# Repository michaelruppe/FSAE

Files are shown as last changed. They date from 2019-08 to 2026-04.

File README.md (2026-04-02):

# FSAE

Hardware projects for the FSAE Electric 2019/2020 competition (Australia).
💻Github https://github.com/michaelruppe/FSAE

## Resources
**Team mentoring and design reviews available - contact through [michaelruppe.com](https://michaelruppe.com)**

[ShutdownCircuit.com](https://shutdowncircuit.com) is a free resource to help new FSAE EV teams shortcut the growing pains of designing EV safety systems.

## [TSAL](TSALv3)
A light that indicates presence of dangerous voltage within the Tractive System

<div align="center">
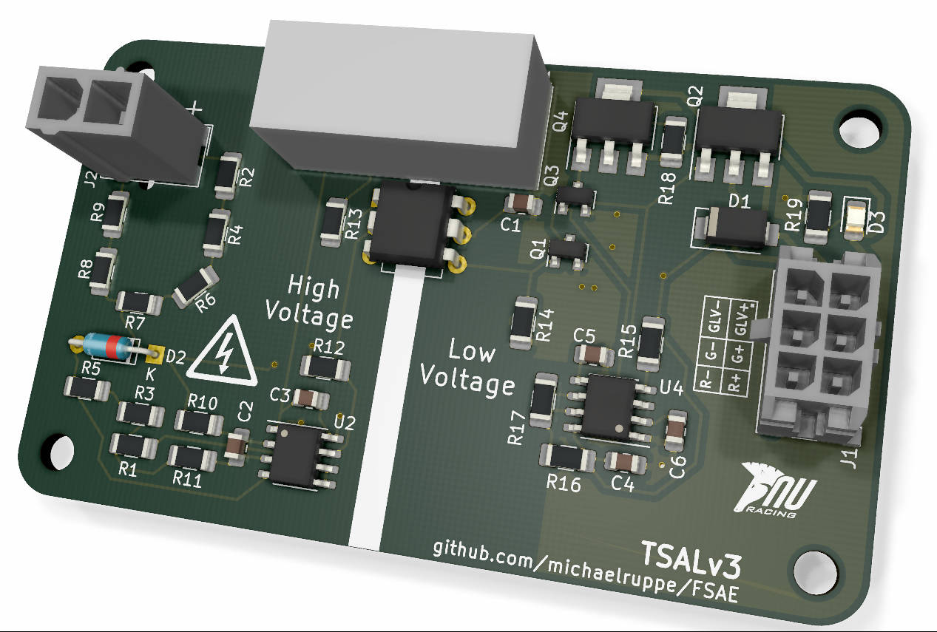
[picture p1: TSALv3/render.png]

<p>The third iteration of the TSAL driver. </p>
</div>

Watch a [video walkthrough](https://youtu.be/bgW9xbbovIY) explaining the circuit operation and design decision.

## [Precharge](Precharge)
A device to precharge the Tractive System. This prototype features voltage feedback to protect AIRs. In open-loop systems, if a wiring fault develops - eg. precharge resistor is disconnected - then the precharge is ineffective and AIRs may become damaged.
<div align="center">
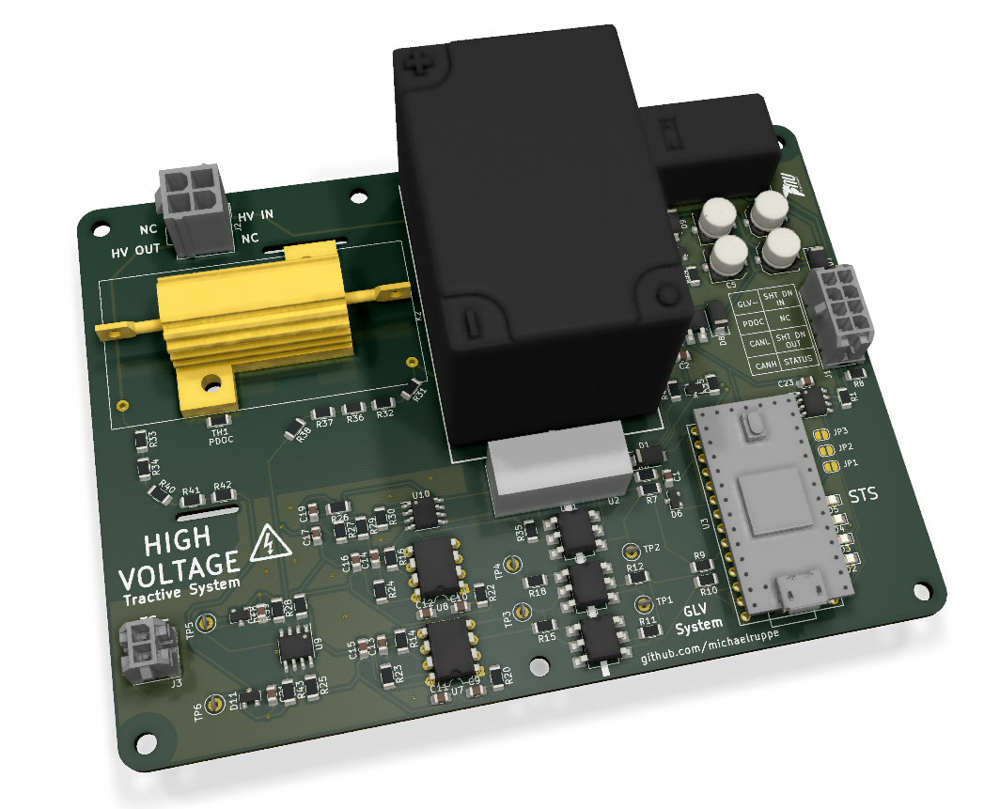
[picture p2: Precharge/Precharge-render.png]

<p>The prototype Precharge module</p>
</div>

 ## [HFL (Hard Fault Latch)](HFL)

 Latches momentary faults that are required to shutdown the EV.

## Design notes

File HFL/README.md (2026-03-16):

**Warning: This design was never physically prototyped. As-is it is a mostly-complete design, but has never been through build, commissioning, troubleshooting. Proceed at your own risk.**

# Hard Fault Latch
A shutdown-circuit component.

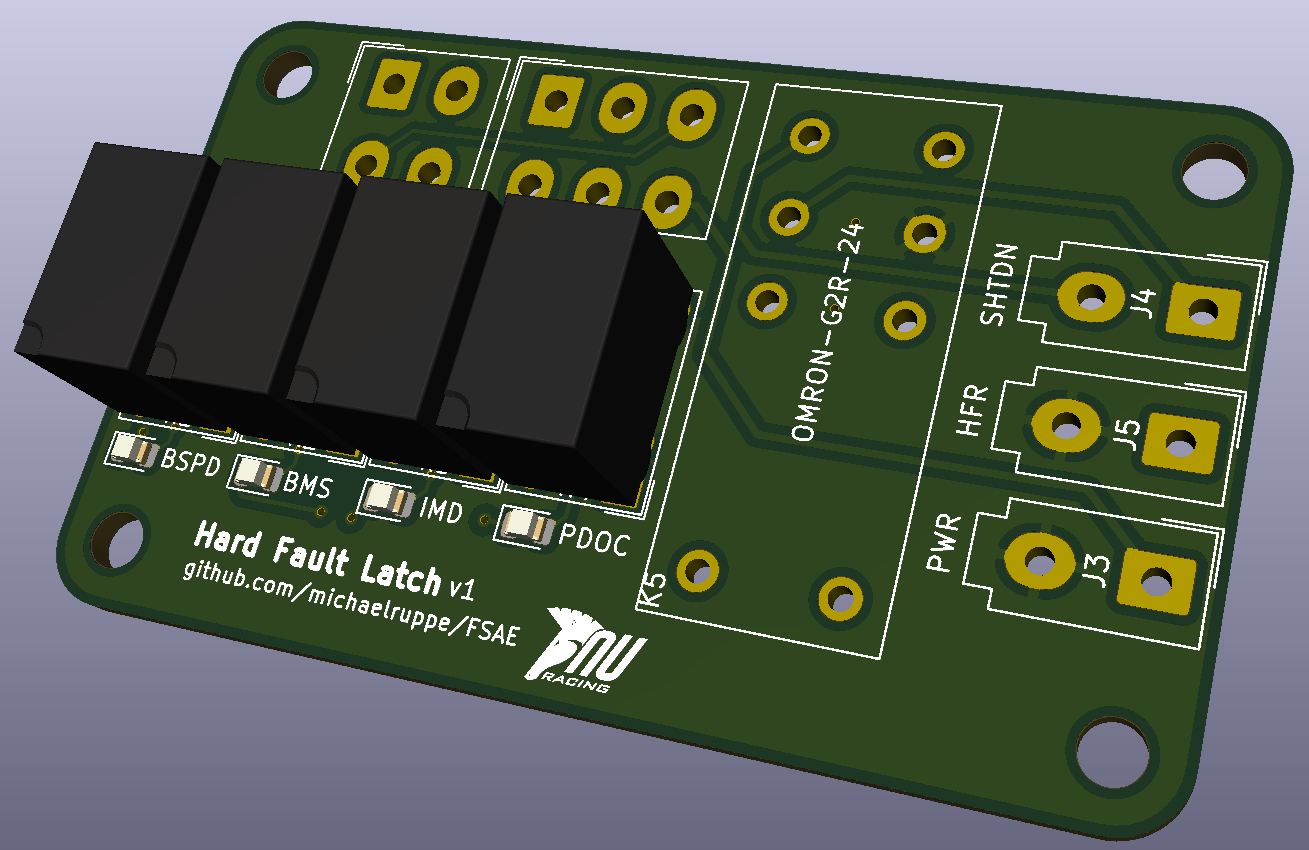
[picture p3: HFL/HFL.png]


The **Hard Fault Latch (HFL)** is a device that breaks the *Shutdown Circuit* when a *Hard Fault* is detected. These are faults generated by the IMD, BMS, BSPD PDOC-temperature, and BOTS. A Hard Fault is any fault that will deactivate the Tractive System, and cannot be reset by the driver.
The HFL is built upon relay-logic because it is easy to understand, reliable and hardened against noise and voltage transients.

An operator must press the HFR button each time the vehicle is powered-on, before the Tractive System can be activated.

Additionally, the HFL passes hard-fault statuses for the IMD, BMS, BSPD and PDOC (**not** BOTS) to the CCU for logging and dash-display.

# Technical Specifications
**ToDo**

# Design Justification
The final output relay must be capable of carrying sufficient current to power an AIR, and be a DPDT type. The smallest readily-available relay found was an OMRON G2R which is rated for 5A.

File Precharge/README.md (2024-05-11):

# Precharge

**[Watch the walkthrough video](https://www.youtube.com/watch?v=6-RndXZ5mR4)**

A device to precharge the Tractive System. This prototype features voltage feedback to protect AIRs. In open-loop systems, if a wiring fault develops (eg. precharge resistor is disconnected or discharge is stuck on) then the precharge is ineffective and AIRs may become damaged.
<div align="center">

<p>Figure 1: The prototype Precharge module</p>
</div>

**Important Directories / Files**
- [code/precharge](code/precharge) - The source code
- [docs/schematic-v1.1.pdf](docs/schematic-v1.1.pdf) - The schematic, as built.
- [docs/pinout-v1.1.pdf](docs/pinout-v1.1.pdf) - Pinout diagram with connection descriptions.
- [docs](docs) - Data collected during commissioning, image assets for this document.
- [Precharge](Precharge) - The PCB design files

## Contents

- [Specifications and Features](#Specifications-and-Features)
- [Operation](#Operation)
- [Commissioning Steps - Precharge](#Commissioning-Steps-Precharge)
  - [Characterise Voltage-Frequency Relationship](Characterise-Voltage-Frequency-Relationship)
  - [Simulate Precharge](#Simulate-Precharge)
  - [Results](#Results)
- [Commissioning Steps - PDOC](#Commissioning-Steps-PDOC)
- [How to modify this design](#How-to-modify-this-design)
- [Recommendations](#Recommendations)

## Specifications and Features
- Wide input voltage 0 - 600V
- Powered by shutdown circuit: 12V
- Integrated PDOC
- Isolated HV measurement
- CAN interface (provisional) for status output
- Serial interface for status and commissioning data
- FSAE one-size-fits-all. This module is capable of precharging any voltage accumulator (within FSAE rules) without significant hardware/software rework. To modify for a new accumulator/tractive-system, select appropriate precharge resistor and update relevant software parameters, discussed in [How to modify this design](#How-to-modify-this-design)

## Operation
A brief description of the Precharge logic follows. Refer to *Figures 2 & 3* for state-flow information.
- Initialise in `State: Standby` and monitor for a stable Shutdown Circuit.
- If Shutdown Circuit is stable, enter `State: Precharge`:
  - Close the precharge relay
  - Monitor Accumulator voltage and Tractive System voltage
  - Once TSV is close enough to AV (eg >95%), precharge is complete
  - If precharge is too fast or too slow, a fault is likely present eg. Wiring fault, discharge stuck-on, stuck relay.
- If precharge completed with no errors, proceed to `State: Online`:
  - Enable the AIR, open precharge relay

If at any point the Shutdown Circuit voltage becomes too low, enter `State: Standby`

<div align="center">
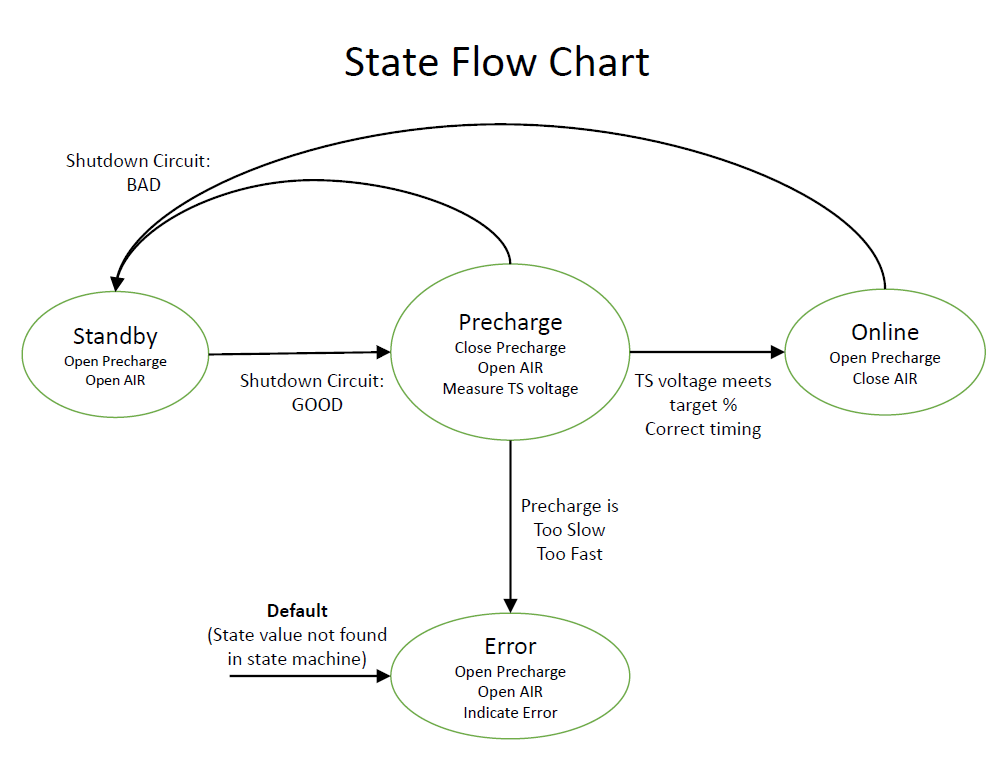
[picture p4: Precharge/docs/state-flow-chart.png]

<p>Figure 2: A top-level look at the state-flow behaviour</p>
</div>
<div align="center">
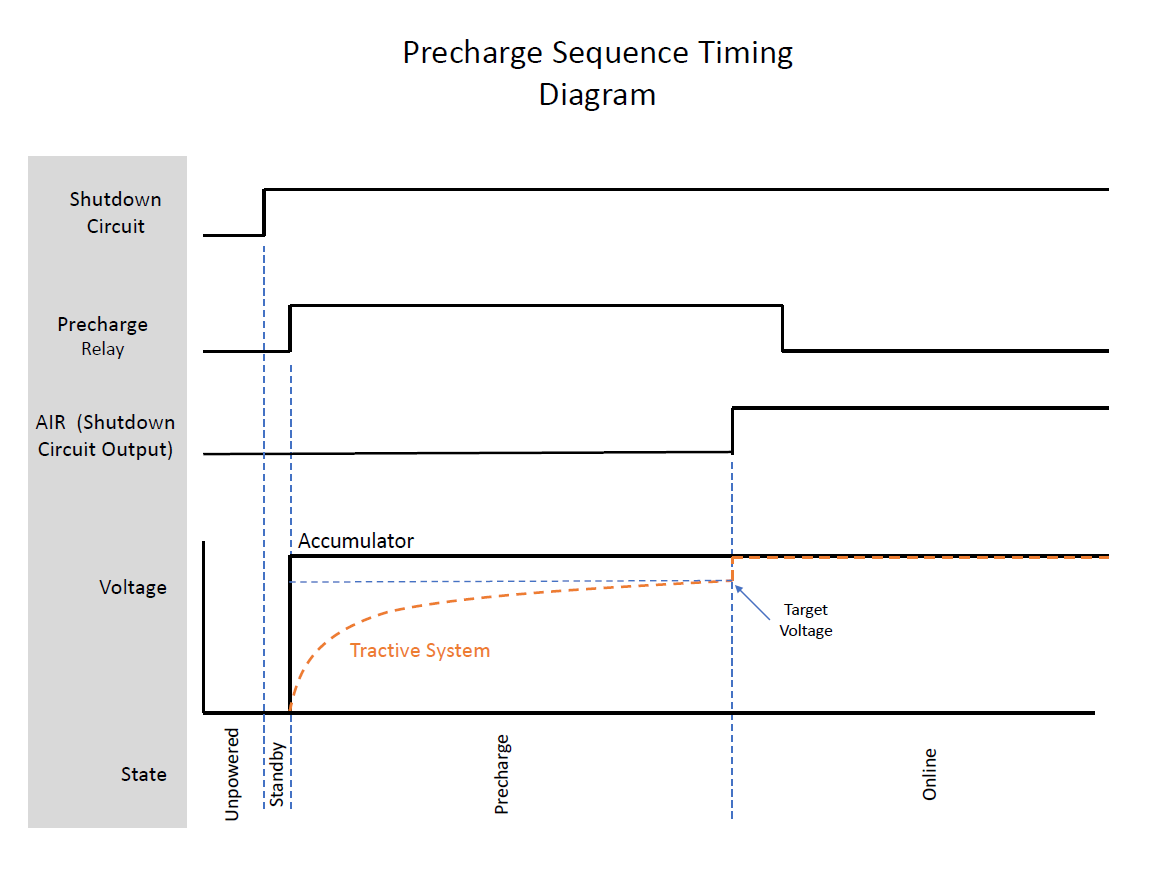
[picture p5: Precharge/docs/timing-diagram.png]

<p>Figure 3: precharge sequence timing. When the TS voltage reaches the target voltage, precharge is complete and the AIR closes. The target voltage should be 90-95% of the Accumulator voltage</p>
</div>

## Commissioning Steps - Precharge
*Refer to the [docs/schematic-v1.1](docs/schematic-v1.1.pdf) for component and test-point references.*

*Refer to [docs/Experiments.xlsx](docs/Experiments.xlsx) for sample data collected during prototype construction.*

This section describes the steps taken to construct and characterise the Precharge Module. Repeat these steps as necessary when re-commissioning later versions of the circuit.

### Characterise Voltage-Frequency Relationship
- Assemble power supply components and V-F converter circuitry `U5 - U9`.
- Characterise voltage-frequency performance: perform V-F experiment `code/01-v-f-experiment` *Refer to Figure 4 for sample data collected during prototype construction*
  - Apply 0.15-10V at V-F inputs: `TP5, TP6`.
  - Record output frequencies: `TP1, TP2` vs input voltages.
  - Create linear fit and record the gain and offset parameters.
  - Update [code/precharge/measurements.cpp](code/precharge/measurements.cpp) with the linear-fit parameters: `V2F_slope_accu, V2F_ofs_accu, V2F_slope_ts, V2F_ofs_ts`
- If resistors `R31,R32,R36-39` or `R33,R34,R40-R3` are different to schematic:
  - Find the gain of these voltage dividers: eg `Gain = R39/(R31+R32+R36+R37+R38+R39)`
  - Update [code/precharge/measurements.cpp](code/precharge/measurements.cpp): `gainVoltageDivider` with the new gain value.

  <div align="center">
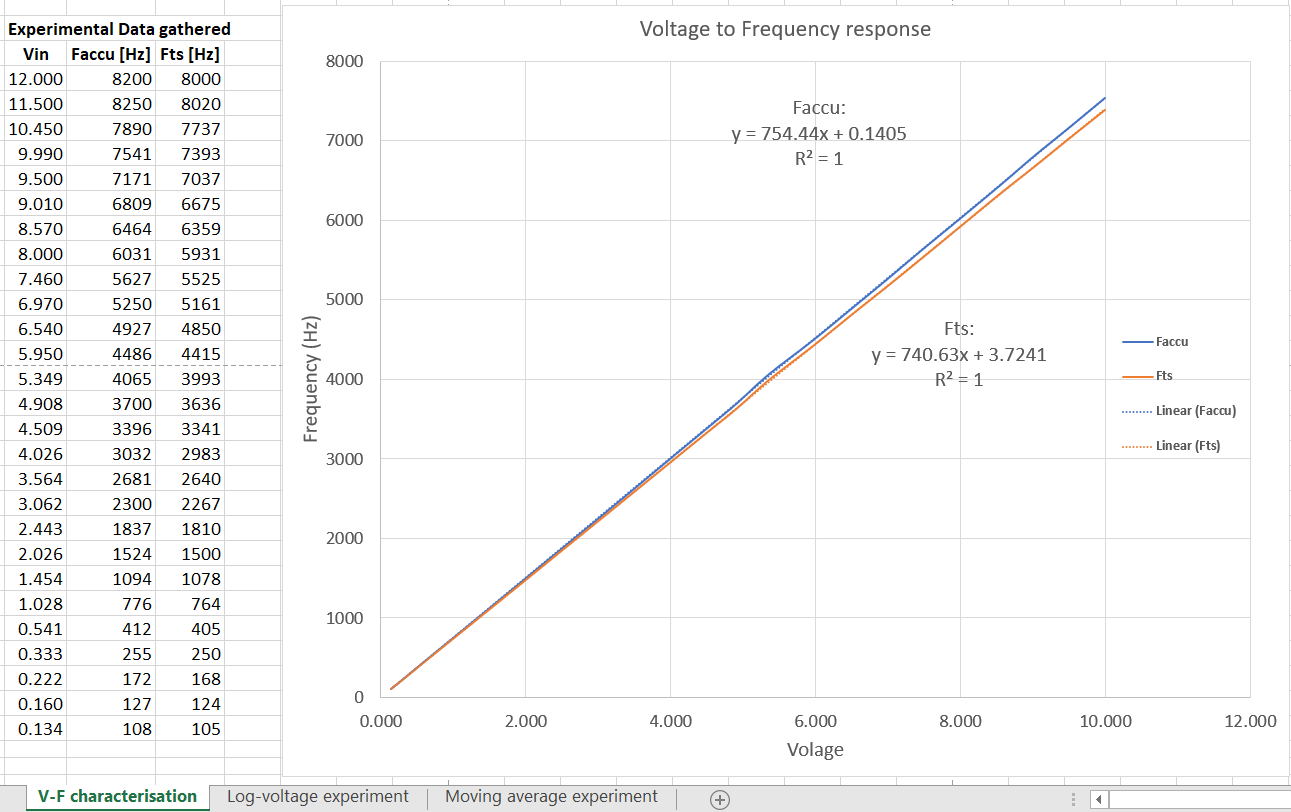
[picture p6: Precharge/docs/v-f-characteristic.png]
  
  <p>Figure 4: Results from the V-F experiment - data collected from the prototype during construction. The V-F response is extremely linear. Expect f(0V) = 0Hz, which is supported by very small y-intercept constants. While the V-F converter circuits are nominally identical, they should be characterised separately to account for component tolerance.</p>
  </div>

### Simulate Precharge
Here, we simulate a precharge sequence using low voltages that bypasses the prescaling voltage dividers.

<div align="center">
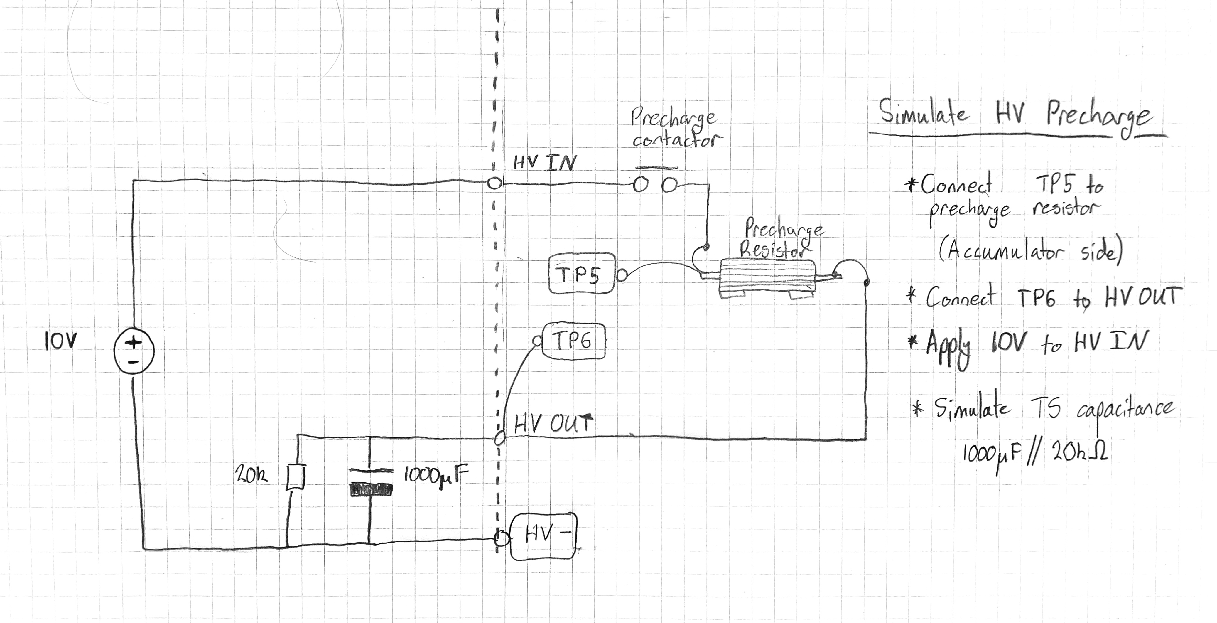
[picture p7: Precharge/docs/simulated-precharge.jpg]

<p>Figure 5: Simulate a precharge sequence using a low voltage. The prescaling voltage dividers are bypassed by connecting Testpoint:TP5 to the switched accumulator voltage; and Testpoint:TP6 to the HV OUT connector.
</p>
</div>

*Voltages listed are referenced to the `GNDS` net, connector `J3` labelled `TS-`*
- Connect a known capacitive load eg 1000uF to `HV OUT`. Include a large parallel resistance (eg 20k) for capacitor discharge.
  - The voltage divider created by this resistance and the precharge resistor `R46` will limit the maximum voltage seen at capacitor. Large resistances will reduce this effect, but the capacitor will discharge more slowly during this test.
- Bypass the prescaling voltage dividers:
  - Connect `TP5` to precharge resistor (accumulator side)
  - Connect `TP6` to `HV OUT`
- Apply 4-10V to `HV IN`. Exact voltage will depend on accumulator voltage to be simulated: Accumulator Voltage multiplied by `gainVoltageDivider` (0.015 from prescribed components) gives this voltage.
- Monitor serial data from the microcontroller via USB
- Power the circuit at `J1`
- Monitor precharge behaviour in serial console and note precharge percentage and duration.
- Modify and upload [code/precharge/precharge.ino](code/precharge/precharge.ino) as necessary. Relevant parameters are:
  - `MIN_EXPECTED`[ms] The minimum allowable precharge time. Times faster than this are likely due to wiring fault.
  - `MAX_EXPECTED`[ms] The maximum allowable precharge time. Times slower than this are likely due to wiring fault, stuck discharge circuit.
  - `TARGET_PERCENT`[%] Precharge to this percentage of accumulator voltage.
    - The discharge resistance used during this simulation affects the maximum TS voltage attainable. I found a maximum voltage of only 90% when using Precharge:390Ohm and discharge 4k7.

### Results
A precharge sequence was simulated following the above procedure with results shown in *Figure 6*. Simulated voltages were measured accurate to the nearest volt.

**Parameters:**
- V Accumulator: 5.05V (336V equivalent)
- Tractive system capacitor: 1000uF
- Tractive system discharge capacitor: 4k7 (connected in parallel with capacitor. Larger value as in Figure 5 is preferred)
- `gainVoltageDivider`= 0.015 ([code/precharge/measurements.cpp](code/precharge/measurements.cpp))
- Target precharge percentage: 88.0 (discharge resistor is only one order of magnitude larger than 390Ohm precharge resistor)

<div align="center">
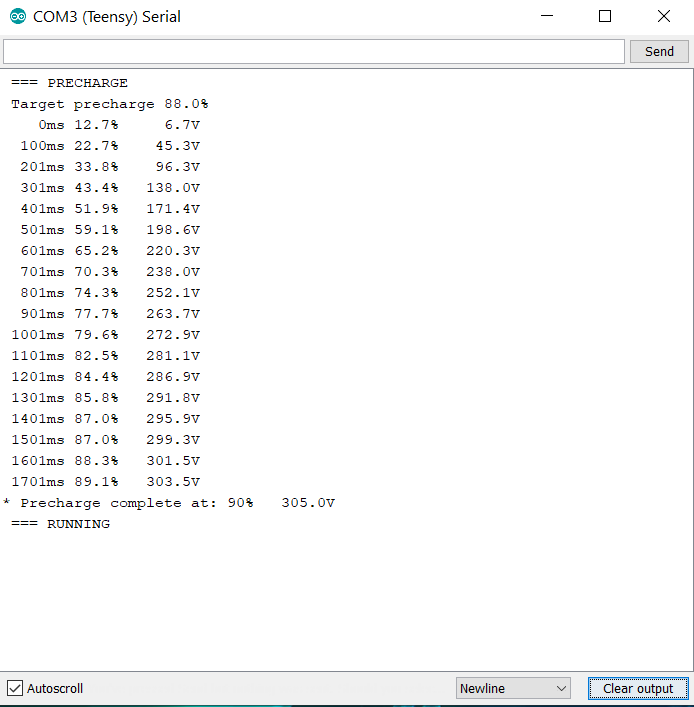
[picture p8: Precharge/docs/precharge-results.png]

<p>Figure 6: Results from a simulated precharge. Here, the accumulator was simulated with 5.05V => 337Vequiv. The TS voltage at TP6 reached 4.561V => 304Vequiv. which is 90.2% as indicated. The precharge finished at 90% instead of 88% because some settling time is imposed by the program.
</p>
</div>

Of note are the seemingly high precharge percentages observed between 0-200ms. These are artifacts of moving average filters used to smooth voltage measurements and reject spurious measurements. Since the smoothed accumulator voltage does not rise instantaneously, the precharge voltage represents a significant percentage in early stages of the precharge cycle.

## Commissioning Steps - PDOC
The Precharge module includes an integrated thermal overload protection (PDOC) (Figure 7). A thermistor `TH1` monitors the precharge resistor temperature. As temperature increases, the inverting-input voltage of comparator `U10A` rises. Once the voltage at the inverting input rises above the reference voltage (noninverting input) the PDOC will trip. The reference voltage created by `R26` and `R27` therefore sets the temperature threshold. If `R27` = `R29` then select `R26` to be equal to the value of `TH1` at the desired trip-temperature. Referring to thermistor data in Figure 8, for a trip-temperature of eg. 80 degC, `R26` should be about 12kOhm.

<div align="center">
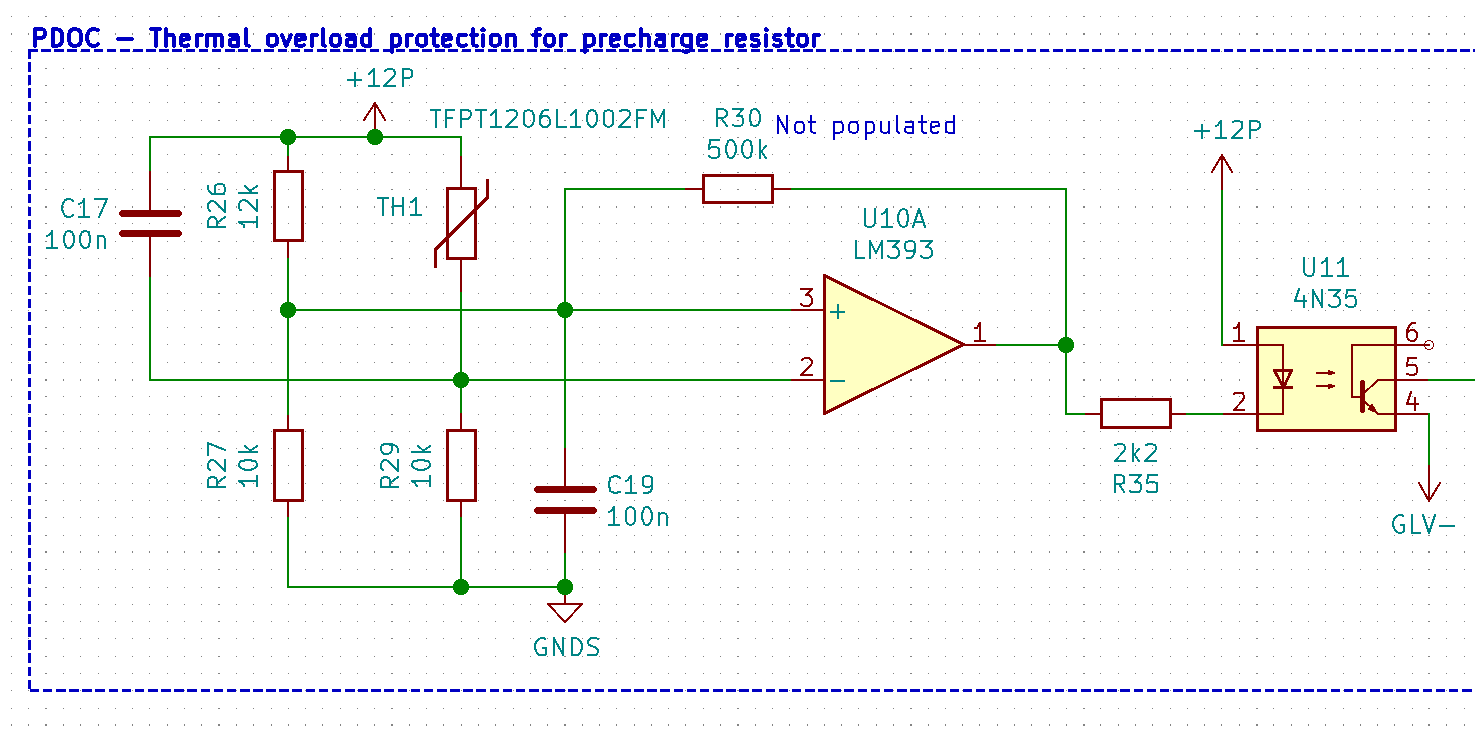
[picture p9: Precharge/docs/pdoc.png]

<p>Figure 7: The Precharge Overload Circuit monitors the temperature of the precharge resistor and triggers a fault if the temperature becomes too high. R26,R27 set the threshold temperature, TH1 is the temperature-monitoring thermistor.
</p>
</div>

<div align="center">
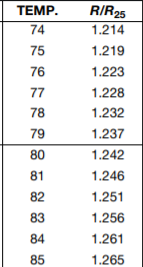
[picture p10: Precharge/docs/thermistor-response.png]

<p>Figure 8: The thermistor response. R_25 is 10kOhm for the selected device. At 80 degrees Celcius the resistance will be 1.242 x 10kOhm = 12.4kOhm
</p>
</div>

## How to modify this design
When moving to a new tractive system configuration and/or accumulator voltage, the only hardware component that may require respecification is the Precharge Resistor `R46`. A HS25 series resistor ([datasheet](datasheets/TE-Connectivity-Type-HS-Series-Resistor-1773035_C)) from TE Connectivity is specified for this component - available in a large range of resistances. As per the datasheet, these devices are capable of short-duration overloads many times in excess of their continuous-duty rating. It is likely that only the resistance will need to be respecified, ie. select a  HS25 family resistor of the appropriate resistance.

<div align="center">
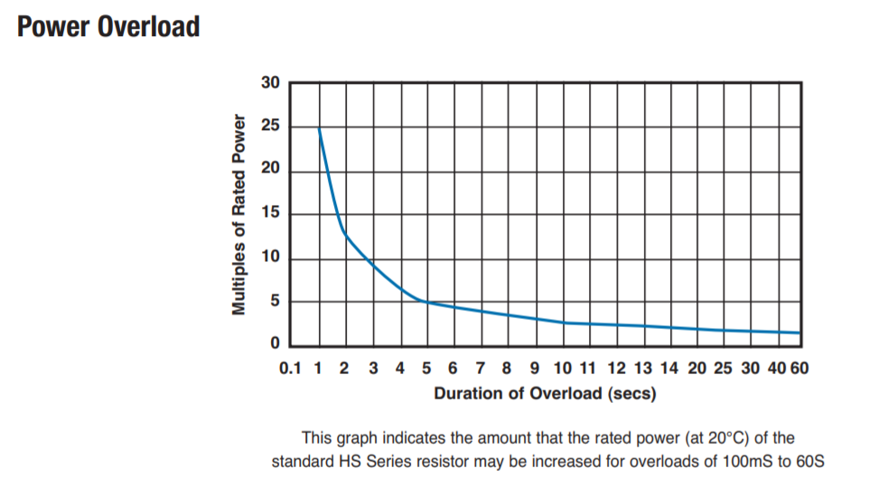
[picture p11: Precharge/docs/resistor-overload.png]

<p>Short term overloading of a power resistor is acceptable. This design relies on short term overloading to keep the power resistor small, light and cheap.
<br>(Graphic Source: TE Connectivity Type HS datasheet)
</p>
</div>

In 2020, NU Racing specified a 400V accumulator and a TS capacitance of 1600uF. Using these as design constraints, a 390Ohm precharge resistor was selected to precharge the TS quickly without excessive overload. As seen below, the resistor is overloaded to 400W (16 times its rating) for a very brief period at the start of a precharge sequence. After approximately 1 second the resistor is no longer overloaded. The initial precharge current(~1A) is well within the capacity of the precharge contactor. The resistance is above the minimum required for 2020 motorcontrollers (47 Ohm).

<div align="center">
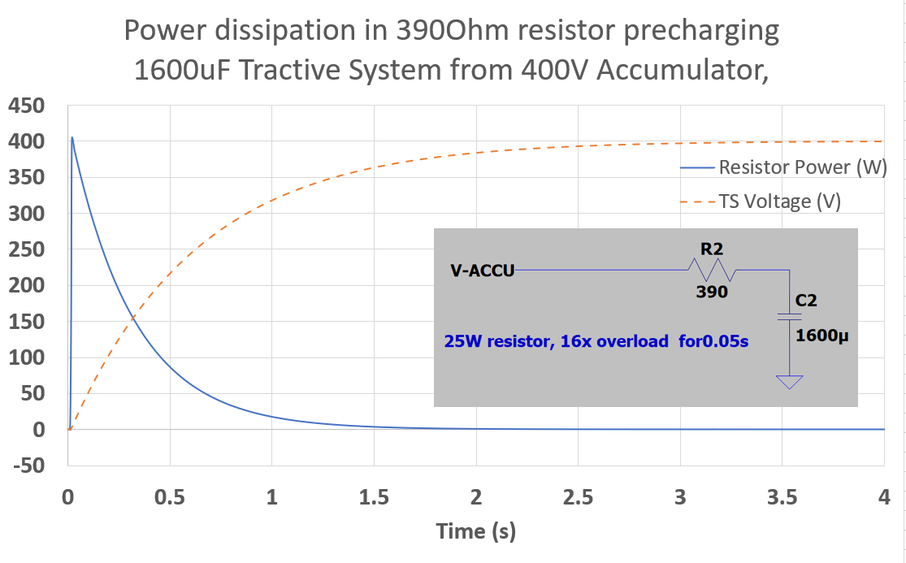
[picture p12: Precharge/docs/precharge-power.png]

<p>A 390Ohm 25W resistor precharges the TS to 95% in about 2.5 seconds, experiencing a brief 16x overload. Overloads of this nature are acceptable for the selected family of power resistors and allow cheaper, smaller, low-power resistors to be specified.
</p>
</div>

Once the appropriate resistor has been selected, follow the [Simulate Precharge](#Simulate-Precharge) steps to identify any software parameters that require modification.

## Recommendations & ToDo

**V-F Conversion**: Either include offset in V-F converter circuit so that min frequency is eg ~100Hz instead of 0Hz ([Datasheet](https://www.ti.com/lit/ds/symlink/lm331.pdf): Figure 14) or replace V-F converters with a microcontroller programmed for the same task. The challenge is that low frequencies require a long timeout period. Applying a 100Hz offset means the longest timeout would be 10 milli-seconds. The current solution works well, using a combination of outlier rejection and Exponential Moving Average filters.

**PCB**:
The footprint assigned to the 4N35 optocouplers is slightly off. Serviceable, but not perfect. Consider re-assigning the footprint.

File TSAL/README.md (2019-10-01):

# TSAL
A comparator-based TSAL design for FSAE Electric 2019
*This repo is for the design of a system required in the Formula SAE competition 2019, and so will use common nomenclature specified in the [2019 rules v2.1](http://www.fsaeonline.com/cdsweb/gen/DocumentResources.aspx)*

The *Tractive System Active Light* is a red/green indicator light that indicates the presence of high-voltage in the Tractive System. The following design for a TSAL driver is split across two modules. The High-Voltage Measurement module (HVM) and the Indicator Module (DRV). The HVM connects to the output of the AIRs, and is located in the accumulator housing. The HVM is responsible for detecting whether Tractive System voltage is above or below the safe threshold.

## System Overview
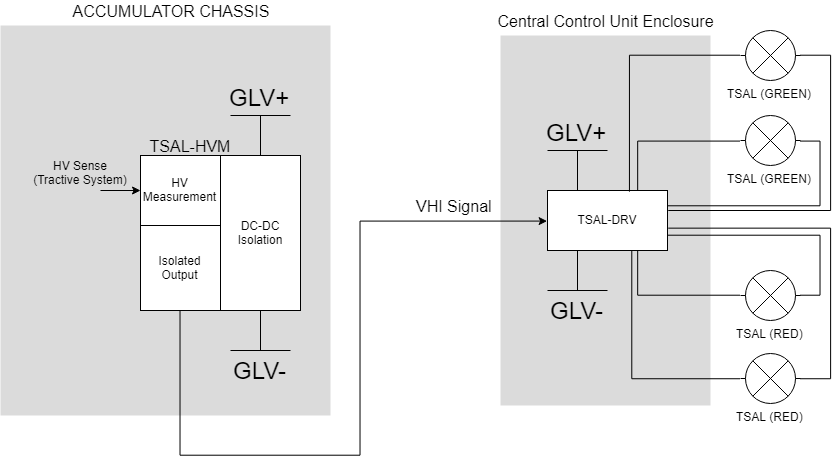
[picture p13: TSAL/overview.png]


## High-Voltage Measurement (HVM)
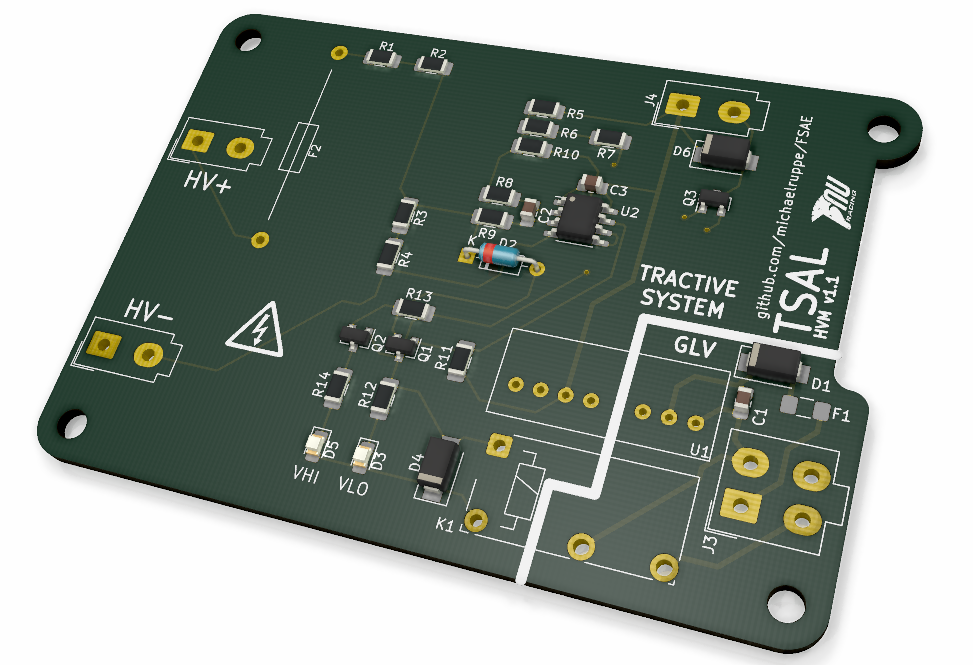
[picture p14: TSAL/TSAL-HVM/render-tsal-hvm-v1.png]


The HVM is located in the accumulator and measures the TS-voltage. The status of the TS-voltage is output by a open-collector style output (switched relay contact to ground).

The HVM has been designed to mount above the IMD, using the same mounting-hole dimensions. This will likely require conformal coating of the board and an intermediate insulating material to meet regulation EV.6.1.5 and EV.6.1.7

The HVM is designed to **not** be user adjustable. Resistive dividers R1, R2, R3, R4 and R5, R6, R7 may be used to set the trigger threshold for the onboard comparator. As specified, the board should safely handle 400V at the HV inputs (untested). Diode D1 begins conducting when approximately 200V is present at HV inputs - effectively limiting the input voltage of the comparator.

### Pinout

| Parameter | Value |
|---|---|
| Max Voltage (HV+ - HV-) | 200V DC |
| Switching threshold (HVin) | 60V DC |
| Supply Voltage | 12V DC |
| Output | Switched Contacts |
| HV < 60V | OPEN |
| HV > 60V | CLOSED |

### Assembly notes
Many parts of the v1 design are provisional.
**ToDo - assembly instructions**

### Design justification
A comparator circuit was chosen because they are relatively simple to design, are well understood and behave predictably.
An isolated power supply U1 is powered by the GLV (12V) and provides an isolated 12V supply for this circuit.

R1, R2, R3, R4 form an input voltage divider which scales the input (0-200V -> 0-12V). The voltage divider is split between multiple resistors to keep the voltage across each resistor manageable. Since each 1208 package is rated for 200VDC this topology is theoretically capable of measuring up to 400VDC. This range can be trivially increased with the addition of more resistors in the divider.

R5, R6, R7 form a resistive divider that provides a stable voltage reference of 3V for the comparator. A resistive divider was chosen over a zener voltage reference because the output of the DC-DC converter U1 should be accurate and stable enough for this application.

With the values chosen, the output of the comparator should be HIGH while input voltage is less than 60V. The output should be LOW for input voltages greater than 60V.

R9, R8, C2 form an input filter for the comparator which is prescribed in the LM311 datasheet. This prevents noise coupling from the output to the input.

R10 is included to provide hysteresis. Since hysteresis is symmetric in this circuit, it is chosen to be small so as not to significantly offset the actual switching threshold from the desired threshold.

N-Channel MOSFET, Q1 and relay K1 form the isolated output of the circuit. While the input voltage is less than 60V, R11 pulls-up the gate of Q1, energising the relay coil and closing the contacts. D3 is a status indicator and D4 is a flyback diode.

The action of Q1 is inverted in Q2 and Q3, which drive an on-board status indicator LED and an off-board status indicator respectively.

To comply with FSAE rules the voltage systems on board are galvanically isolated. The clearances on-board require it to be conformal coated.

### Failure Modes - Fail Unsafe
 - Should the output of comparator U2 become disabled, R12 will continually pull the gate of Q1 high, energising the relay coil and indicating that a safe voltage is present.
 - If J1 is disconnected the TSAL will continually indicate a safe voltage is present - regardless of whether this is true or not.

These failure modes are clearly undesirable but deemed an acceptable risk for a first-revision TSAL. No publicly available design was found from competing teams that addressed these limitations.
The reasons these modes are fail-unsafe is due to the action of the comparator: The particular comparator chosen (LM311) has an open-collector output which must be accompanied by a pullup resistor. Since the switching action of the comparator pulls the output low and is capable of driving a relay directly, a suggested improvement is to either drive the relay coil directly (which also inverts the output action). This would reduce the parts count, removing Q1 from the BOM and reduce the number of critical components. Alternatively, a comparator with a push-pull output could be selected and directly substituted for U2.

### Failure Modes - Fail Safe
 - Should the TSAL-HVM lose power, the coil of relay K1 will be de-energised and its contacts will open. This will continually signal that dangerous voltage is present in the Tractive System. While that may not necessarily be true, the implausible behaviour of the TSAL should alert engineers that a fault is present: Either the AIRs are stuck closed, the Tractive System capacitors are remaining charged or a fault is present in the TSAL. All of these plausible causes should warrant due caution.

### Recommendations
There is significant room for improvement of the TSAL-HVM as made clear by the failure modes listed above. Here I will outline a brief description of how one might address what I consider to be the most serious limitation: The tendency to indicate safe-voltage if the TSAL-HVM is disconnected from the Tractive System.

If one can assume that the Tractive System is always capacitive (large capacitors at the motor driver power-input) then the HVM may be redesigned to check for the presence of capacitance at its measurement terminals using the Grounded Specimen Test method.

## Indicator module (DRV)
The Indicator module is powered by the GLVS and controls the behaviour of the red/green TSAL. It is controlled by a single input which is pulled low by the action of the HVM. Each output channel is capable of several amps and should be suitable for driving 12V LED assemblies or even incandescent bulbs.

### Pinout

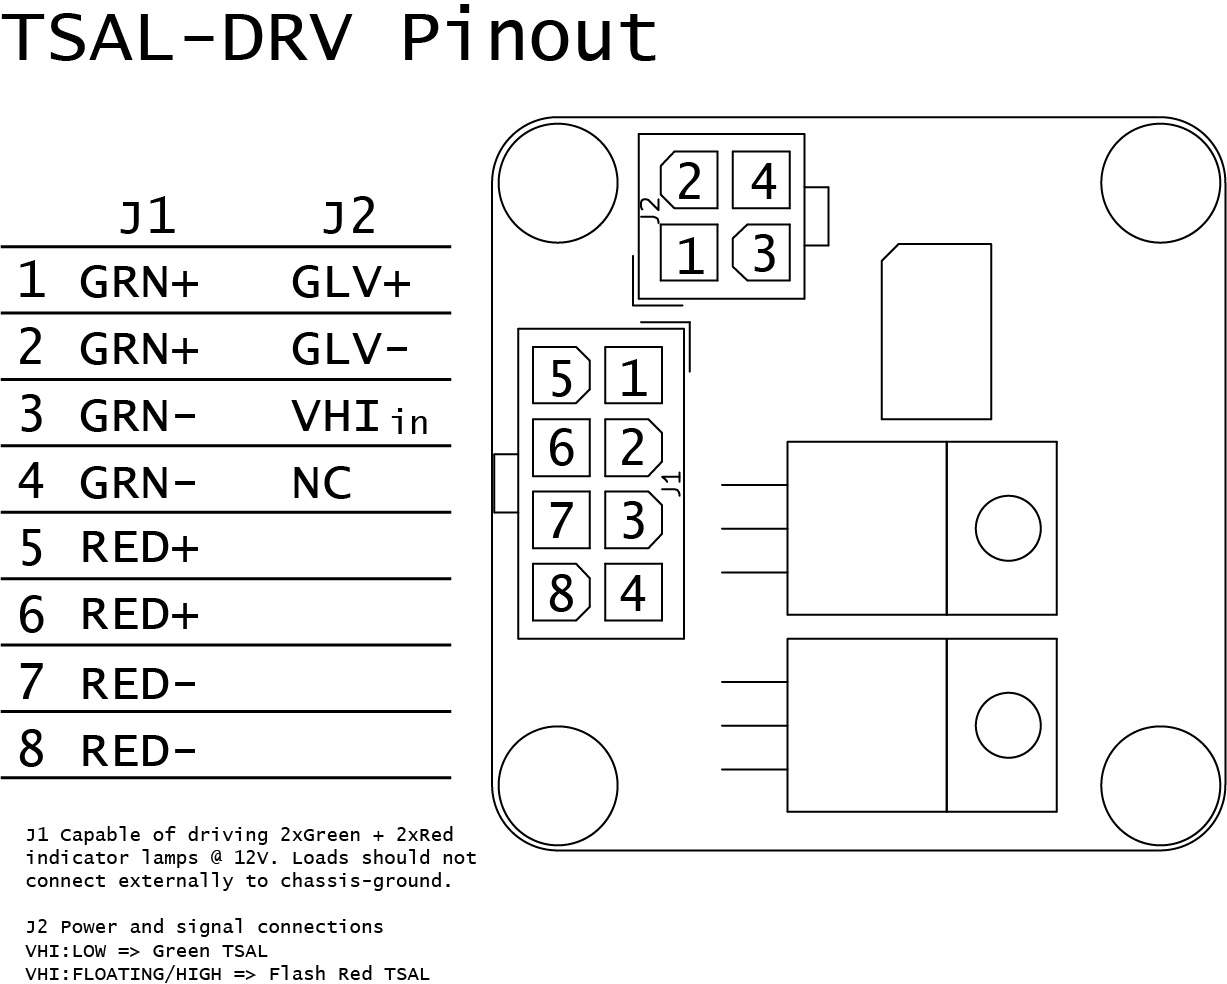
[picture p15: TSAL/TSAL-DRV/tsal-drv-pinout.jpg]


### Design Notes
The heart of the driver module is the complementary operation of the timer (U1) and the P-Channel MOSFET (Q1). The VHI signal effectively selects which of these components should be active.

When VHI (J2) is pulled to ground, Q1 switches on - driving VLO indicator LED (D2) and powering the offboard, green TSAL LEDs (J1). A low signal at VHI also holds the reset pin of the U1 low, disabling its output.

When VHI is floating (the output-relay on HVM is open), R2 pulls-up the gate of Q1, turning off Q1. The RESET pin of U1 is also pulled-up, activating U1 which oscillates at approx. 3Hz, oscillating Q2 which flashes VHI LED (D1) and the off-board red TSAL LEDs (J1).

Power to the TSAL-DRV is unregulated, since all components are sufficiently robust to handle power deviations from the expected 12V.

### Known issues
The two power MOSFETs are a little close together. So close in fact that they could feasibly touch given the tolerances of fasteners and 3.2mm drilled holes.
Nothing should be *immediately* damaged if the tabs of the MOSFETs touch. However, any difference in switching time will cause momentary high-current through both transistors whenever the state of VHI changes. This is because the MOSFET drains will be connected together so there will be a momentary current path from GLV+ through Q1, Q2, to ground during any overlap in switching time.

Operation of the red/green circuit blocks are not *strictly* complementary. It is feasible that some analogue voltage could be applied at VHI which would allow both red and green components of the TSAL to be active. This is not a concern under the prescribed operating conditions. The operation could trivially be made strictly complementary by including input conditioning to VHI.

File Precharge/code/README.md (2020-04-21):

# Precharge Source Code

There are several code projects here, each maturing as the prototype is commissioned.
The library source files have evolved as the prototype evolves - eg. measurements.cpp
from one project will not be the same as another.

## Projects listed by maturity
- [01-v-f-experiment](01-v-f-experiment/) Used to measure the characteristics of V-F converters
- [02-log-voltage](02-log-voltage/) Using the data obtained in the v-f expermiment to log voltage information
for TS and Accumulator in a precharge bench-experiment
- [03-log-voltage-EMA](03-log-voltage-EMA/) The same as `02` but now an Exponential Moving Average class is included to filter voltage data - virtually removing spurious peaks entirely.
- [precharge](precharge/) The final precharge program.

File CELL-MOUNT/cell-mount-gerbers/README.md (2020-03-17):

# Cell Mount

*A fiberglass plate for mounting cells in EV.One (2019)*

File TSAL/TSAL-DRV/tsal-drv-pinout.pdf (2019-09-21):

# TSAL-DRV Pinout

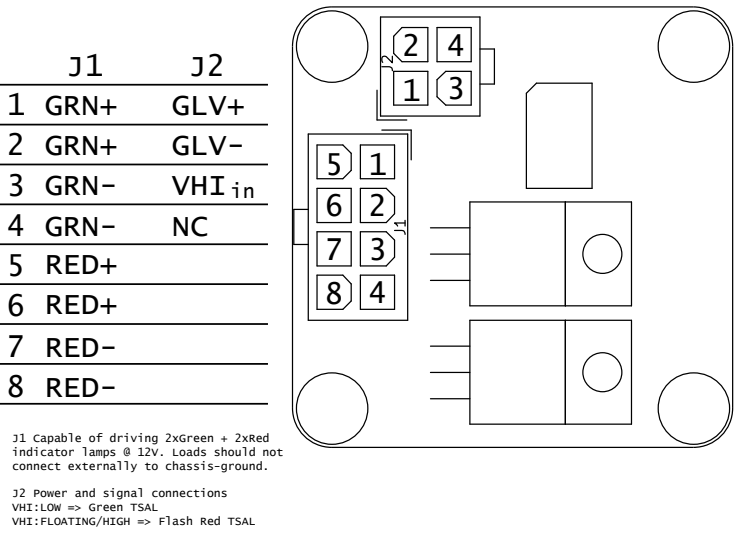
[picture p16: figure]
GRN+; GLV+; GLV- VHI NC; GRN+ GRN- GRN-; RED- RED-; RED+ RED+; J1 Capable of driving 2xGreen + 2xRed indicator lamps @ 12V. Loads should not connect externally to chassis-ground.; J2 Power and signal connections VHI:LOW => Green TSAL VHI:FLOATING/HIGH => Flash Red TSAL

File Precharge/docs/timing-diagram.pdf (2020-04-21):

Shutdown
Circuit

Precharge
Relay

AIR (Shutdown
Circuit Output)

Accumulator

Tractive System

Voltage

Unpowered
Standby

Precharge
Online
State

## Precharge Sequence Timing Diagram

Target
Voltage

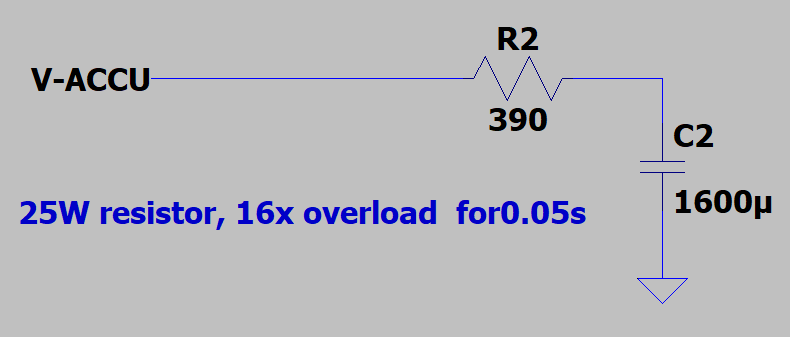
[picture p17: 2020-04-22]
Precharge/docs/precharge-400V-390ohm-schematic.png

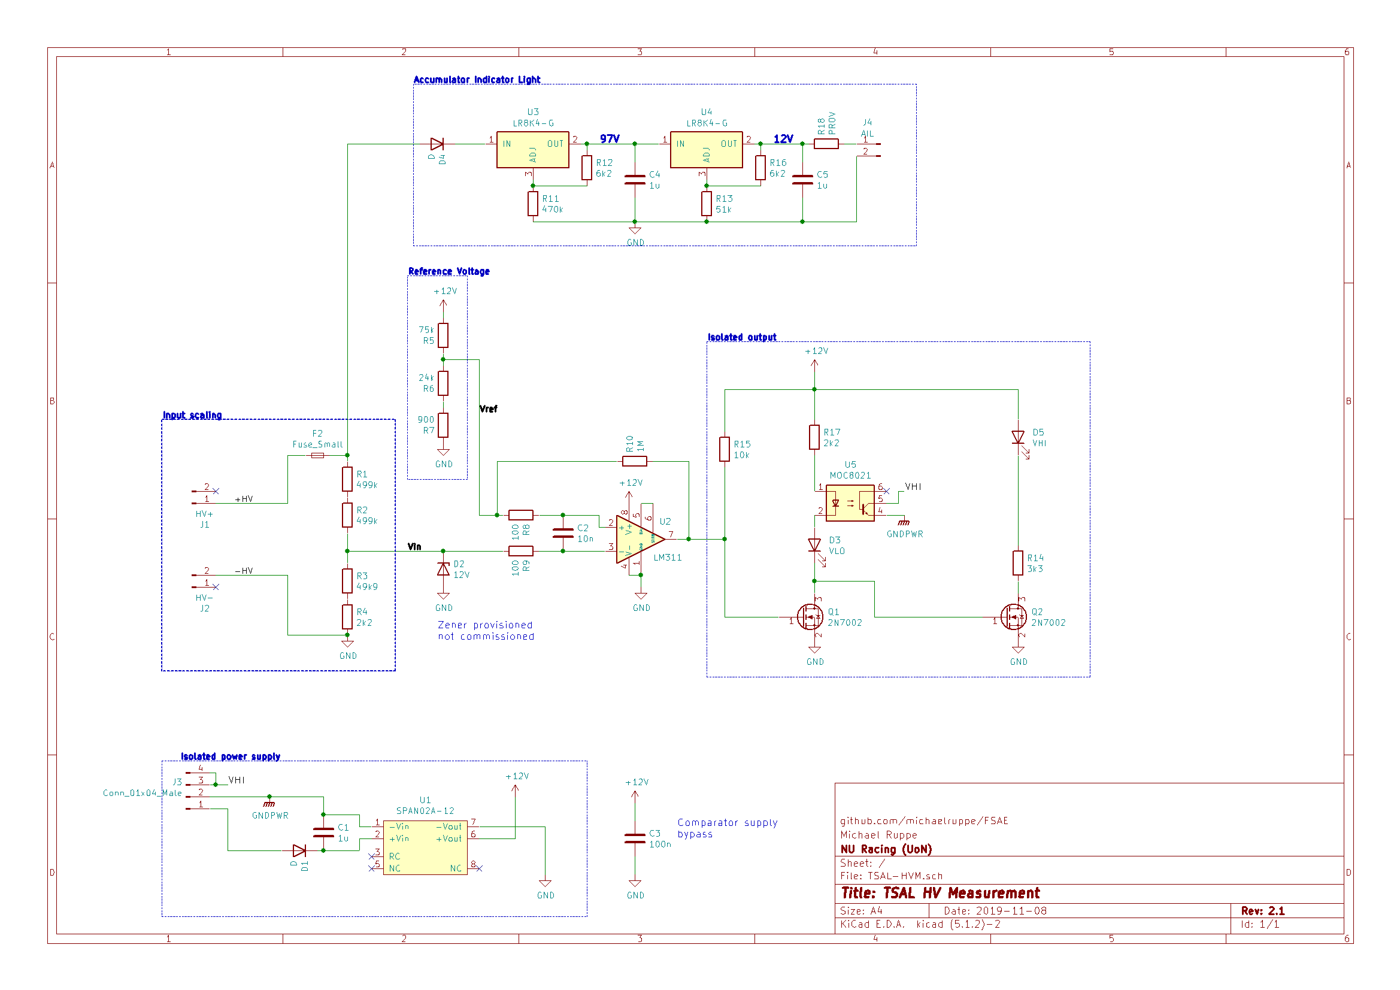
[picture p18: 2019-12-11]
TSAL/TSAL-HVM/schematic-tsal-hvm-v2.1.png

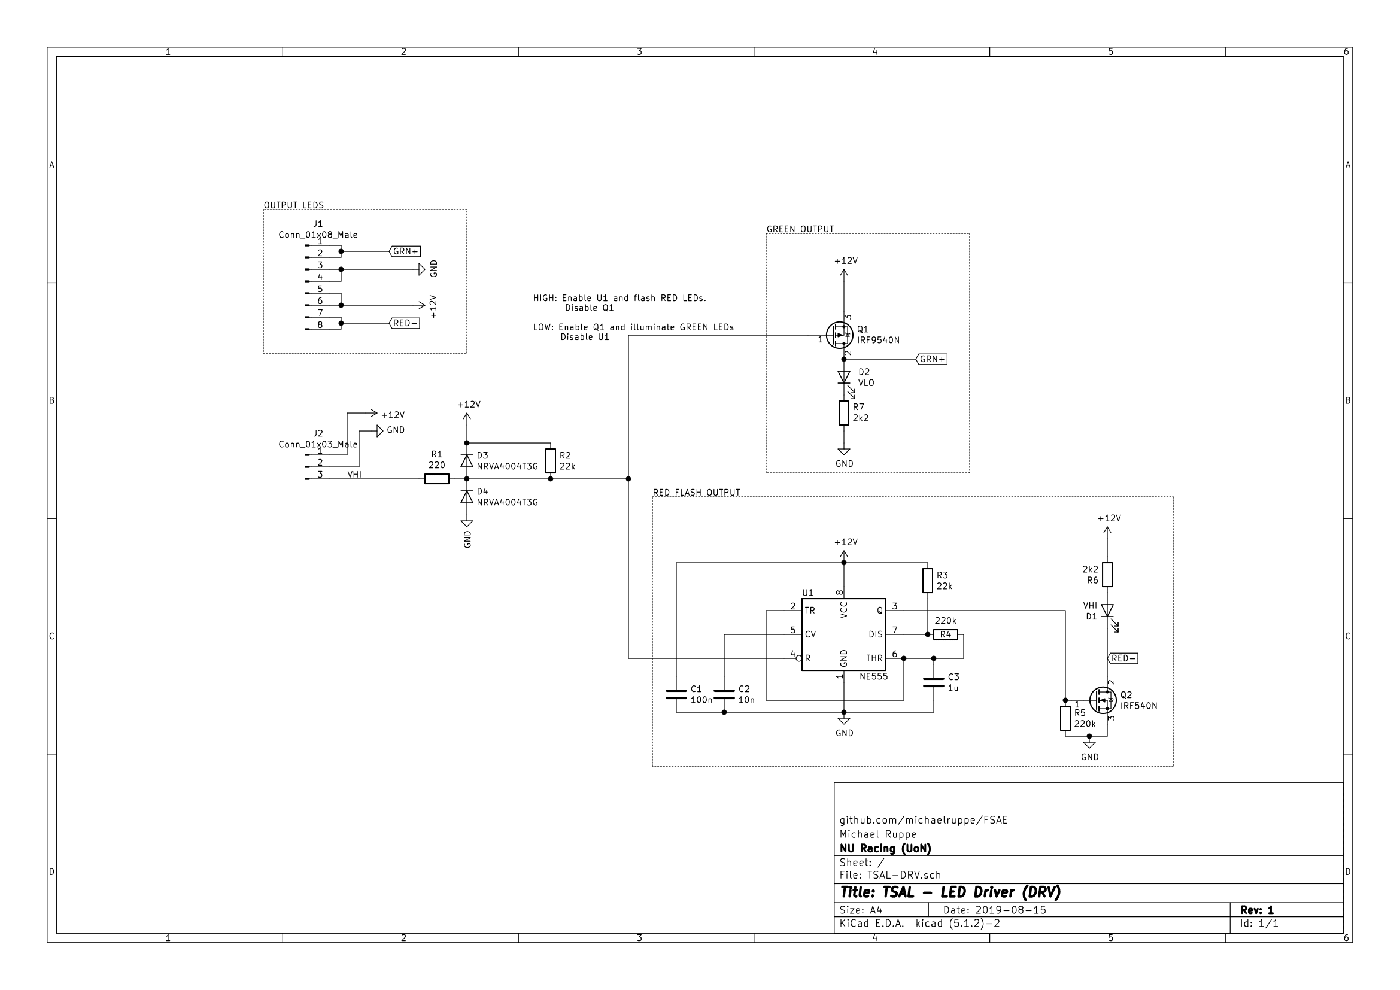
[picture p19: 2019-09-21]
TSAL/TSAL-DRV/schematic-tsal-drv-v1.png

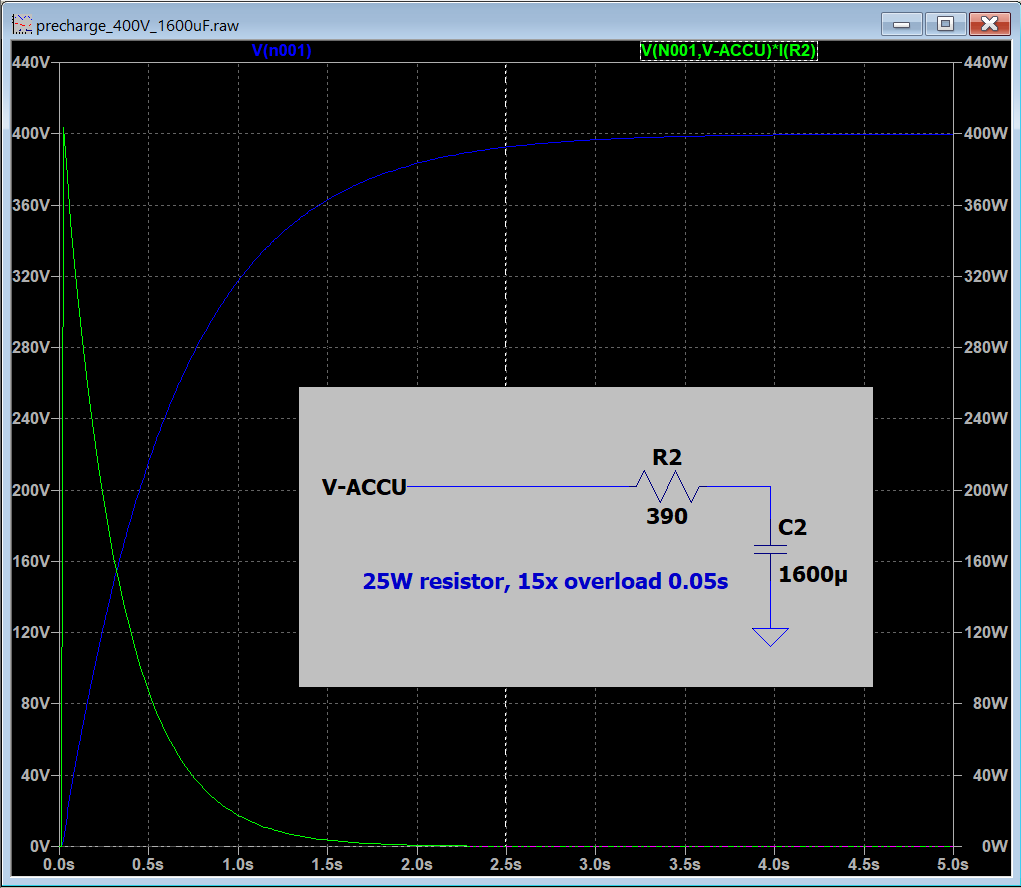
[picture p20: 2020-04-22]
Precharge/docs/precharge-400V-390ohm-simulation.png

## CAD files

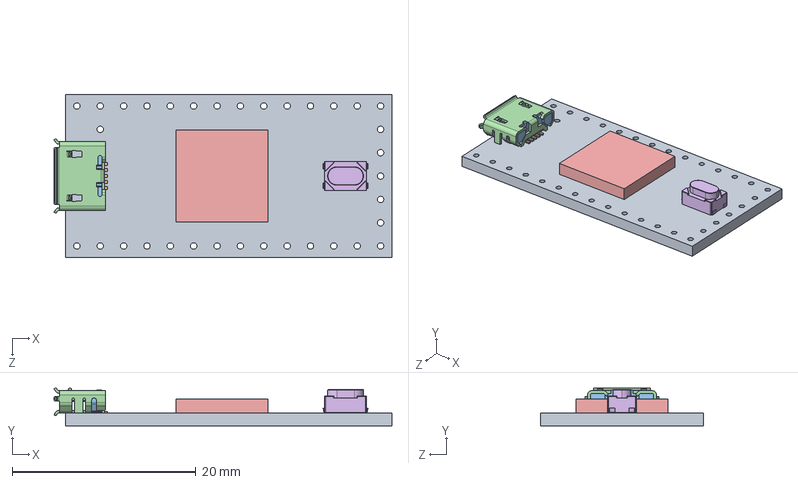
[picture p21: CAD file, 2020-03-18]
Precharge/Precharge/CAD-files/Teensy_4.0_Assembly.STEP
36.8 x 4.12 x 17.7 mm
Teensy_4.0_PCB
Micro USB-B Female 5Pin SMD
NXP iMXRT1062
SKRPACE010 v4

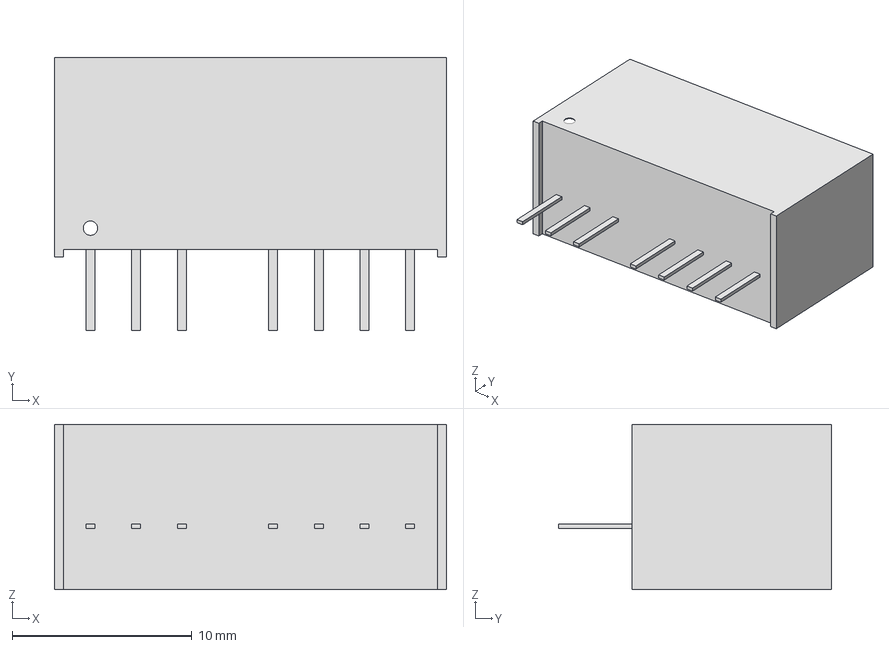
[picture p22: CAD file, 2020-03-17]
TSALv3/CAD files/SPAN02.step
21.8 x 15.2 x 9.20 mm

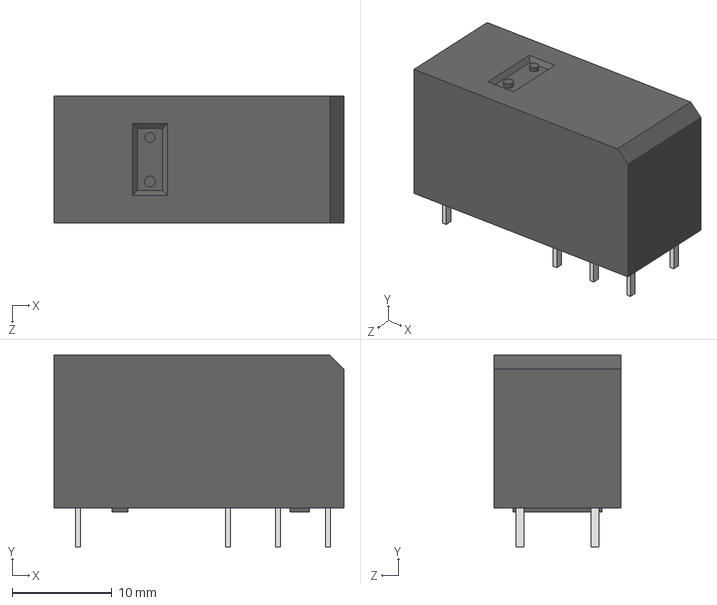
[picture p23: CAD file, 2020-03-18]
Precharge/Precharge/CAD-files/G2RL_24.step
29.0 x 19.2 x 12.7 mm

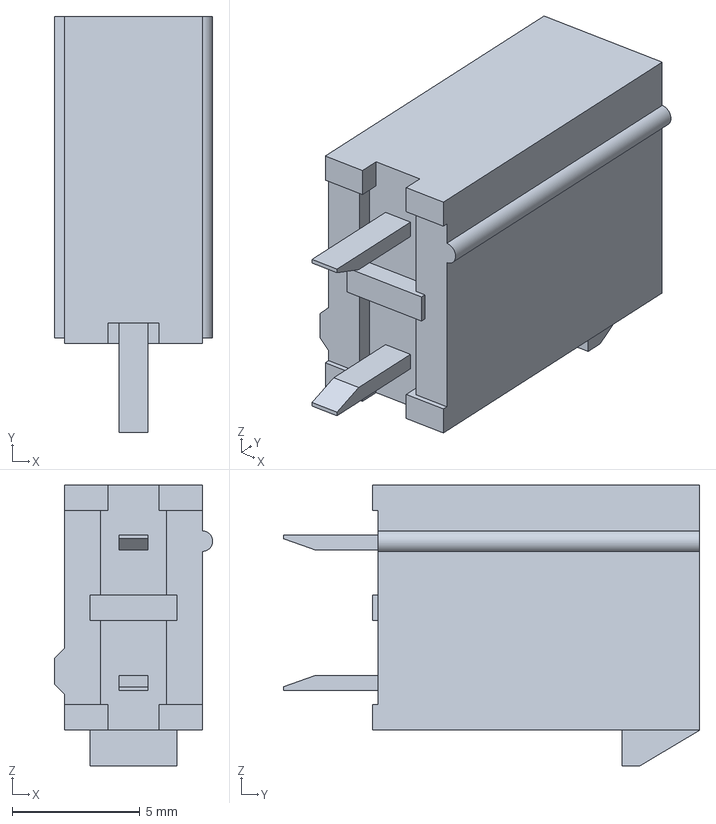
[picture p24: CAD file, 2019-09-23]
TSALv3/CAD files/2-pin-minifit-jr.stp
6.20 x 16.3 x 11.0 mm

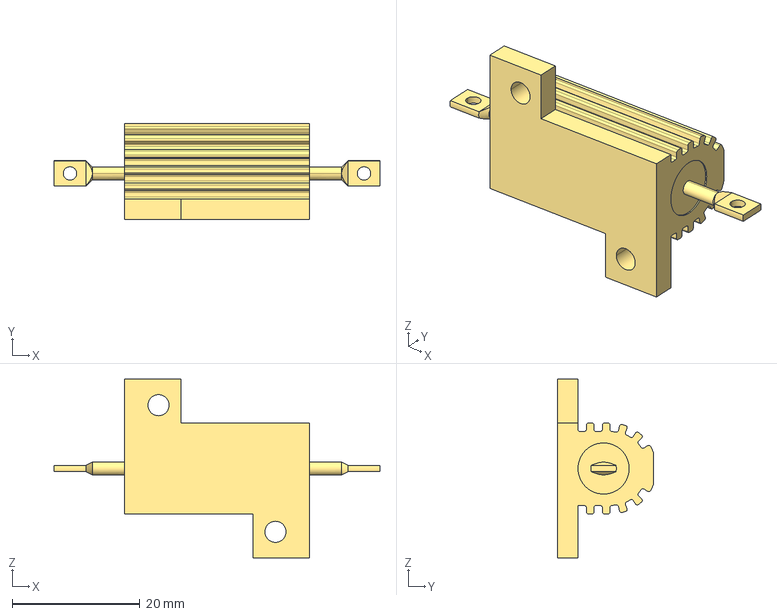
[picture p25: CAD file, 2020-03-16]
Precharge/Precharge/CAD-files/HSA25.igs
51.0 x 15.0 x 28.0 mm

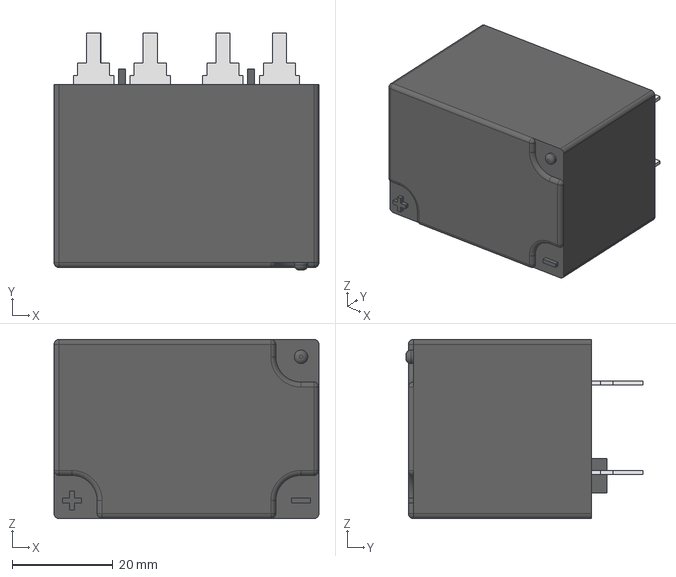
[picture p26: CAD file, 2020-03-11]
Precharge/Precharge/CAD-files/G7L_2A_X.stp
52.5 x 47.0 x 35.5 mm

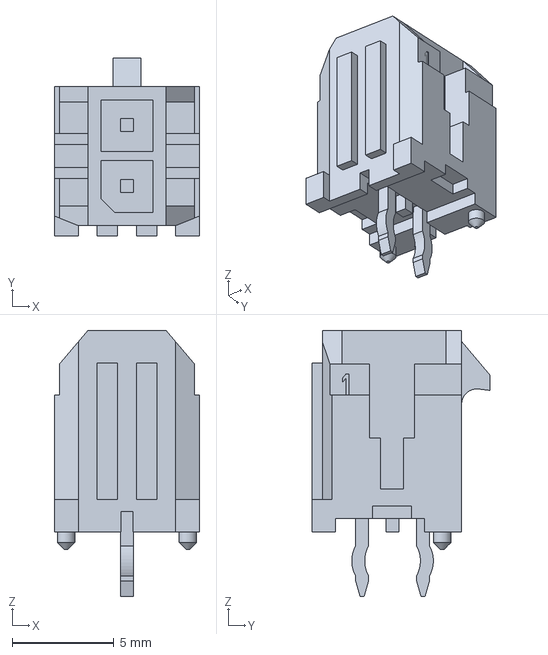
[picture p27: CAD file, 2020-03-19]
Precharge/Precharge/CAD-files/430450212.stp
7.15 x 8.77 x 13.1 mm

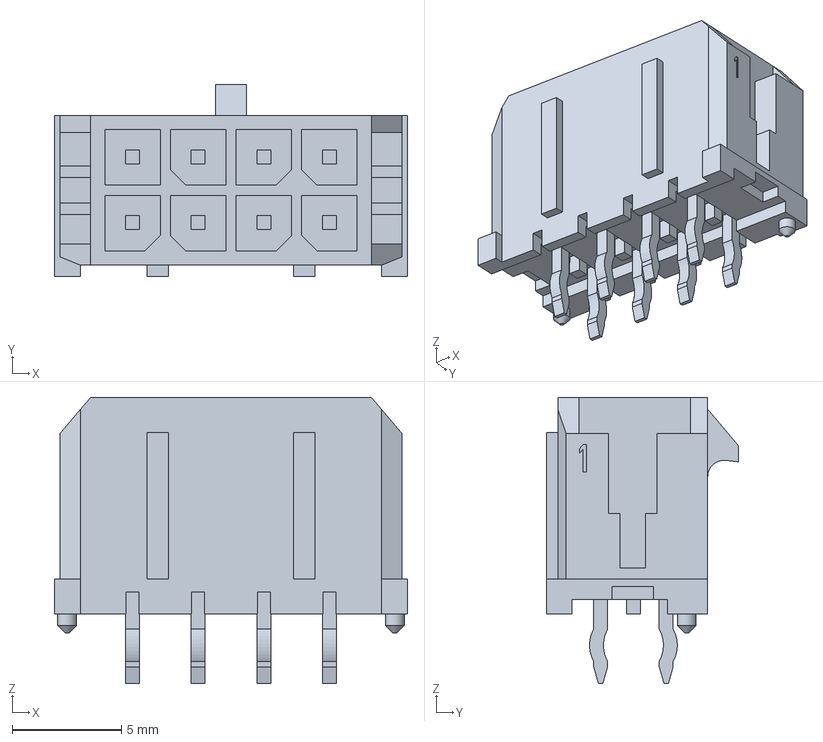
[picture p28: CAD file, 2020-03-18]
Precharge/Precharge/CAD-files/430450812.stp
16.2 x 8.77 x 13.1 mm

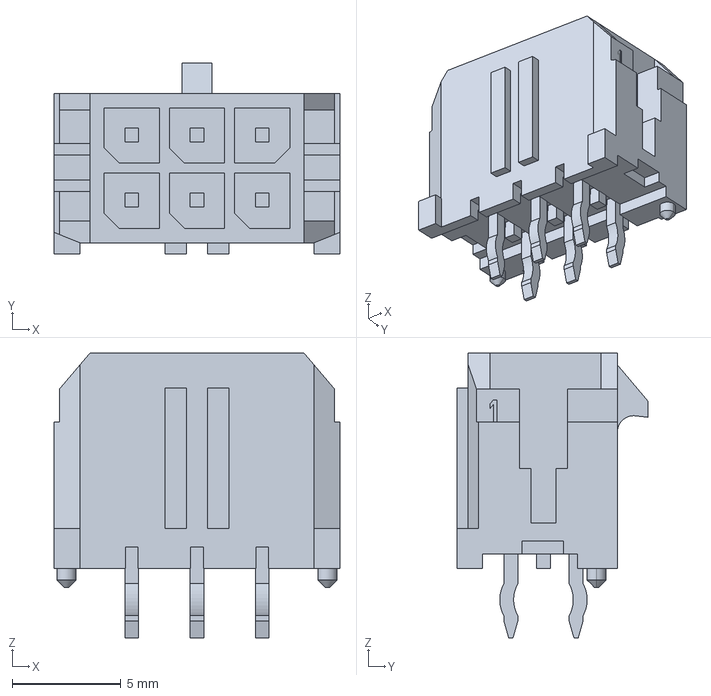
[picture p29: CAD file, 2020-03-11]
TSALv3/CAD files/430450612.stp
13.2 x 8.77 x 13.1 mm

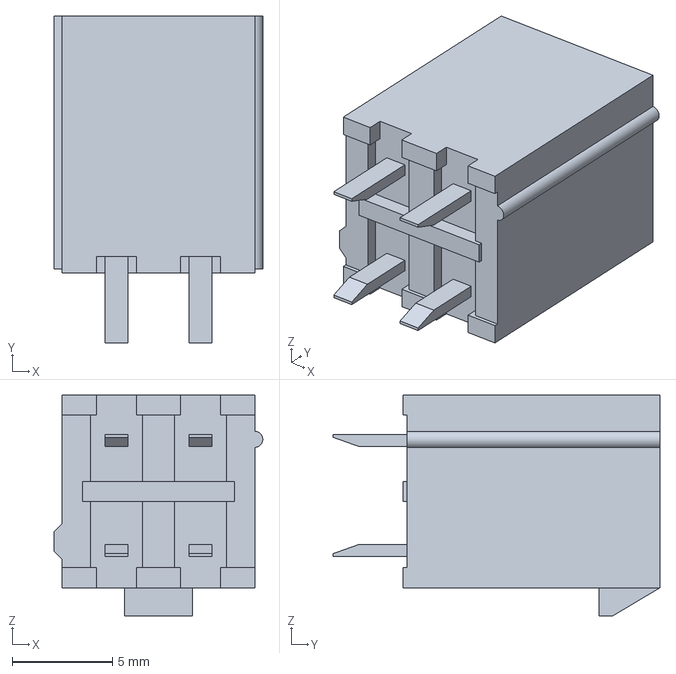
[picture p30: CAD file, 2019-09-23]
Precharge/Precharge/CAD-files/39281043.stp
10.4 x 16.3 x 11.0 mm

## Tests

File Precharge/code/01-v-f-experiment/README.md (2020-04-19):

# V-F characterisation

This program is for performing the V-F characterisation experiment.

### How to perform the experiment
- Apply voltage at `SchematicRef: TP5 and TP6` from 0 to 10V
- Record the frequencies that are logged to the console
- Perform linear fits to the collected data: y = mx + b
- Populate the relevant constants in the main program with the linear-fit constants you found in the previous step.

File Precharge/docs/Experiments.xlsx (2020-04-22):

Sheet: Precharge SPICE simulation
time | Resistor Power (W) | TS Voltage (V) | I(R2)
0 | 0 | 0 | 0
0.01 | 0 | 0 | 0
0.01001933312 | 0.001533361 | 1.324067e-05 | -0.00198285
0.01003875694 | 0.006162031 | 5.410287e-05 | -0.003974931
0.01006465535 | 0.01714794 | 0.0001560603 | -0.006630918
0.01011645219 | 0.05562289 | 0.0005211794 | -0.01194248
0.01022004587 | 0.1985613 | 0.001896134 | -0.02256395
0.01042723322 | 0.7482008 | 0.00722411 | -0.04380027
0.01084160793 | 2.900998 | 0.02818591 | -0.08624649
0.01167035734 | 11.40844 | 0.1112816 | -0.1710334
0.01332785617 | 45.13331 | 0.4417524 | -0.3401859
0.01664285383 | 178.882 | 1.585441 | -0.6772531
0.02 | 403.7442 | 3.187406 | -1.017468
0.03257764739 | 387.8121 | 11.09549 | -0.9971911
0.04515529479 | 372.4933 | 18.85388 | -0.9772978
0.05773294218 | 357.7698 | 26.46256 | -0.9577883
0.07031058957 | 343.6242 | 33.92155 | -0.9386627
0.08288823697 | 330.0393 | 41.23083 | -0.9199209
0.09546588436 | 316.9982 | 48.39041 | -0.901563
0.1080435318 | 304.4845 | 55.40029 | -0.883589
0.1317600496 | 282.2687 | 68.20969 | -0.8507444
0.1554765675 | 261.609 | 80.58257 | -0.8190191
0.1791930853 | 242.4221 | 92.51892 | -0.788413
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

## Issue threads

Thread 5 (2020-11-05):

Pre-charger / Dis-charger

DavidDast, 2020-11-05:
Hi, Michael, I'm a student at a university in Sweden where I got the task to make the pre-charger
I made this in google in drive: https://docs.google.com/spreadsheets/d/1Iv6vfXVOTpihR3HI_DqoE699ijv5pMhWjXgmG9TUZTQ/edit?usp=sharing

The issue is what kind of circuit do use and what other components do I need?
I need some guidance.

kind regards David.

DavidDast, 2020-11-11:
Or do you have any recommendation where to buy the circuit board

michaelruppe, 2020-11-12:
Hi David, I can't access your link.
If you're looking for a pcb manufacturer there are plenty of options for small scale: JLC Pcb,  Pcbway etc

michaelruppe, 2020-11-12:
If its the first precharge for your team, I'd go with a simple timer-based one.

DavidDast, 2020-11-13:
oh sorry here is the working link:
https://docs.google.com/spreadsheets/d/1Iv6vfXVOTpihR3HI_DqoE699ijv5pMhWjXgmG9TUZTQ/edit?usp=sharing

Yes, it is the first time we build it, and not so familiar with building circuits but in the link, I have the parts that I think we need.

DavidDast, 2020-11-16:
I also have a problem to find a company that has a capacitance of 12000uF and over 111V and that only sell in small amounts do you know a company that I can order from?

DavidDast, 2020-11-18:
Sorry for the spam of Questions, but what did you use to download the code to the circuit?

michaelruppe, 2020-11-19:
> Sorry for the spam of Questions, but what did you use to download the code to the circuit?

The hardware is a Teensy 4.0.
PJRC has a guide on using Teensy with the arduino IDE.

> I also have a problem to find a company that has a capacitance of 12000uF and over 111V and that only sell in small amounts do you know a company that I can order from?

I don't. Why do you need to buy this capacitor? Do your motor drivers not come with integrated capacitors?

DavidDast, 2020-11-23:
Yes we have but they are at 100uF and we have hub motors I don't know if that changes anything? is it enough to just use one of the motor's capacitor at 1000uF and then just ramp up the resistor?

But it seems a bit strange to have a cable go from the pre-charger to one of the hub motors that are placed near the wheel and then back to the pre-charger? then just having a capacitor in the circuit board.. just wondering

DavidDast, 2020-11-25:
Oh sorry, now I understand I feel so dumb, yes we can connect them to the motor controllers with their capacitors.

michaelruppe, 2020-11-27:
I'm a little confused - help me understand.
Your motor drivers already have (presumably sufficient) capacitance at their power input. Have you determined they need additional capacitance? Is that where the figure 12000uF is coming from?
I'm afraid I can't be much help at the moment.

What is your current working idea? Perhaps a drawing/schematic would help.

DavidDast, 2020-11-30:
Sorry for the confusement we found that the motor controllers had 2616uF each and what we are thinking about is connecting the 2 motor controllers capacitors and use them so together we have 5230uF, so we calculated that it would take 2.6s to pre-charge to 95%

The schematic we have for pre-charge and dis-charge

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

DavidDast, 2020-11-30:
The 12V system is actually one system but in the schematic its two parts

DavidDast, 2020-12-03:
I updated the excel drive link also

Closed 2024-05-11.

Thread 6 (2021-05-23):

Pre charge & discharge

abdoahmed0509, 2021-05-23:
Hi, Michael, I'm a student at a university in Ain-shams (Egyptian University).
So, I got the task to make a pre-charge circuit.
I only have an issue with the resistance value this my calculations. Can u have a look at them?
my system is 100V and with 4 Motor controllers each (4000uf)
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

Closed 2021-07-25.

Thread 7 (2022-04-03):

TSAL V3

Dmat10, 2022-04-03:
Hi Michael,

I hope you are doing well. I am an FSAE student in Canada, and our team is currently in need of a TSAL board. Unfortunately, the member responsible for the design of the TSAL is no longer with us and left little documentation for us to pick up from. I came across your TSAL walkthrough video, and I would like to ask we could implement your TSAL V3 design for our vehicle with due credits, of course. I would appreciate your response.

Thank you.

michaelruppe, 2022-04-05:
Of course! This whole repo is MIT licensed - you're free to remix and reuse anything as you see fit.
Best of luck!

Closed 2022-04-05.

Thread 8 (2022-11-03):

Adjust TSAL threshold

jucarla, 2022-11-03:
Hello Michael, I am planning to ude an adapted version of your TSAL, but I want to adjust the voltage threshold from 60V to 40V. Any idea of how can I do this?

michaelruppe, 2022-11-21:
Hi! The tsal driver is a comparator circuit - change the reference voltage and you'll tune the switching threshold.

Closed 2024-05-10.

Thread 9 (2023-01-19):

TSAL R12

steinkjn, 2023-01-19:
Hi Michael,

Thanks for these great designs! My team was reviewing the TSAl v3 design and was wondering about the purpose of R12? Any guidance would be appreciated.

michaelruppe, 2024-05-11:
R12 is a hysteresis resistor. It is not necessary and can be omitted. In fact, I never populated this in the final build because I preferred to reduce the risk of high voltages appearing at the opamp.

Hysteresis is only really important for high speed circuits generally. This is just a visual indicator hysteresis is not needed - chatter on the output is inconsequential

Closed 2024-05-11.

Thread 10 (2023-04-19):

Suspected Typo in Precharge - How to modify this design

bazmn, 2023-04-19:
@michaelruppe Hi Mate,

Under michaelruppe/FSAE/tree/master/Precharge#how-to-modify-this-design

You reference the need to change the 'Precharge Resistor R49.'

I don't believe you were referencing R49 but instead R46. I don't see a need to modify R49.

Instead R46 is the HS25 series resistor like you reference.

michaelruppe, 2024-05-11:
Fixed!

Closed 2024-05-11.

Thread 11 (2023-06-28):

Documentation for our team

jfulreader64, 2023-06-28:
Hello,
Our TSAL design uses your schematic and just have replaced the MOSFETs in the circuit. I am documenting all our circuits and am wondering if you are okay with me posting our tsal pcb and linking to your channel and github. Your video was very informative and taught me a lot about electronics.  The readme and schematic will note that it is your design if you are okay with this!
Thanks,
John
Clarkson Formula Electric knights

michaelruppe, 2023-07-03:
Of course! This is an open source project and MIT licensed. All the videos are accessible in the public domain and can be linked/embedded as you like.
Glad you found it useful :v:

Closed 2023-07-03.

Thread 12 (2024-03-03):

Comparator getting too hot

10120860nQ50, 2024-03-03:
Our schematic for our TSAL for our FSAE team is attached to this, our issue is that the comparator gets too hot when testing the board, the green LED turns on at first then stops when the comparator gets hot, and the red LED doesn't turn on or flash at all. None of us can figure out what the issue with this is
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

michaelruppe, 2024-03-05:
Hi! This all looks about right.
I should say that I didn't populate R12 positive feedback resistor in my design since hysteresis is not really important and I thought it might make things more complicated.
Perhaps that's the case here? Or the comparator was damaged during commissioning or testing from an errant short?
Want to post some close up shits of your hardware version? It may be a soldering issue

10120860nQ50, 2024-03-06:
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

This is what our board looks like with everything soldered on

michaelruppe, 2024-03-07:
Have you already replaced the comparator? It could have just been destroyed by an earlier mistake that had already been resolved. It looks like there could be some risk of solder bridging some pins now - perhaps in the past there was a dead short on the output

michaelruppe, 2024-03-07:
Sanity check that the comparator is the right way around too - I can't tell from the photo if it is placed in the correct orientation

10120860nQ50, 2024-03-07:
Yes, the comparator was upside down at first so we took it off and soldered on a new one, but we were still running into the same issue of it getting too hot

michaelruppe, 2024-03-08:
I'm not sure what else I can comment on aside from general debugging help.
- Probe your net voltages to check they make sense
- check for shorts between pins. There is a fair amount of solder whiskers littering the board, especially around the comparator.
- if the comparator gets hot, it's almost certainly destroyed. Remove it and measure net voltages, clear shorts, try again.

Do you understand how the circuit ought to operate well enough from the video? Removing the comparator you should be able to test the important voltages on the comparator inputs. You can also drive the output manually to check the output circuit works as intended.

Get Outlook for Android<https://aka.ms/AAb9ysg>
________________________________
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

Closed 2024-05-11.

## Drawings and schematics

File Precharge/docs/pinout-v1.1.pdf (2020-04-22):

## Precharge v1.1 Pinout & test-points

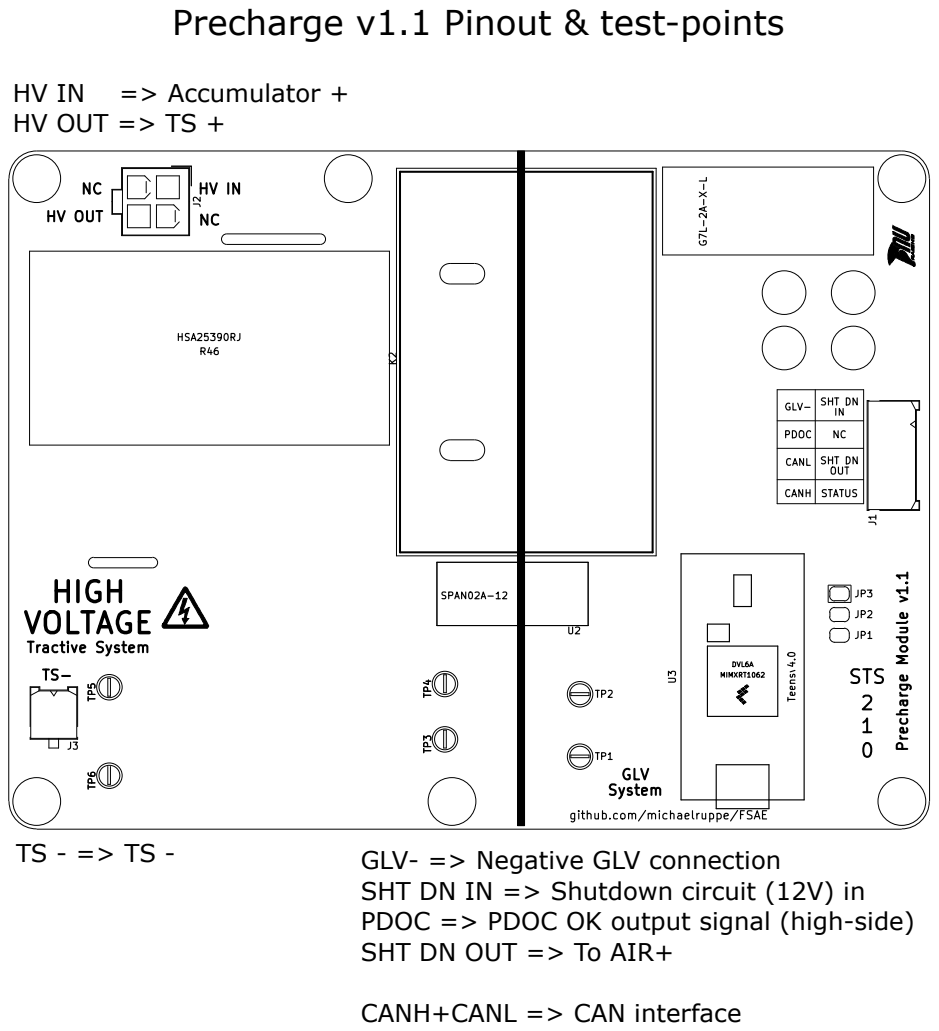
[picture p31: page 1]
GLV- => Negative GLV connection

HV IN => Accumulator +
HV OUT => TS +

SHT DN IN => Shutdown circuit (12V) in
PDOC => PDOC OK output signal (high-side)
SHT DN OUT => To AIR+

CANH+CANL => CAN interface

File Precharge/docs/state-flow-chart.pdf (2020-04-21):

# State Flow Chart

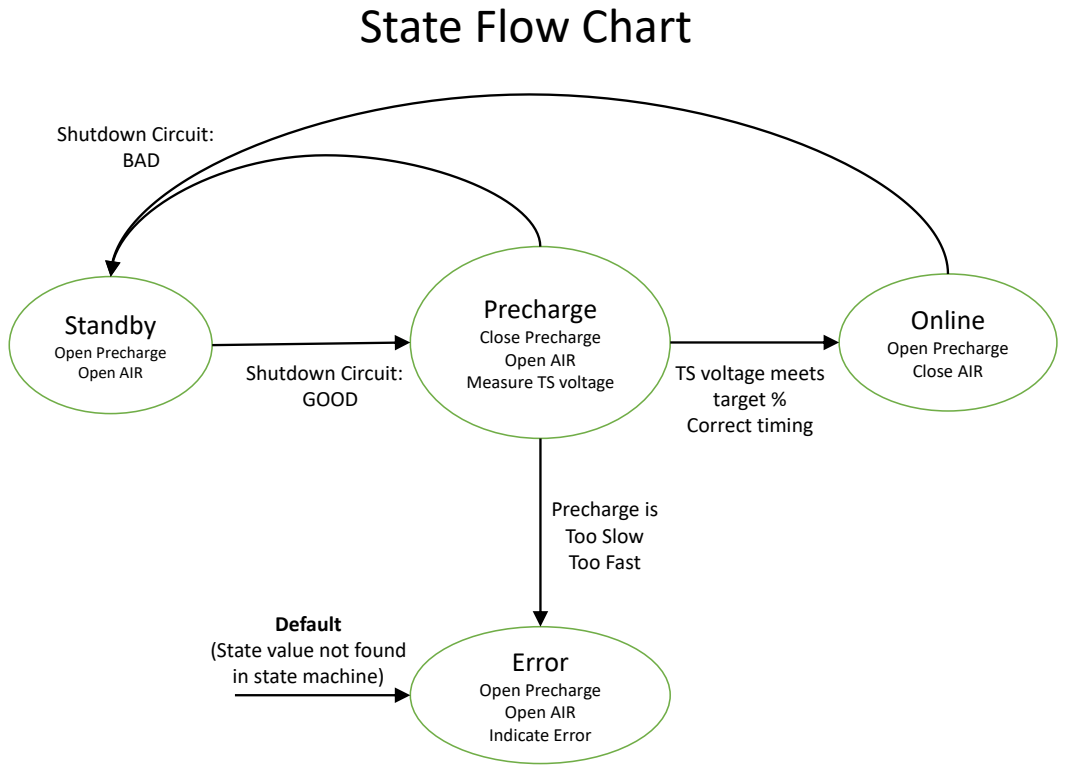
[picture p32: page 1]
Standby; Open Precharge Open AIR; Online; Open Precharge Close AIR; Error; Open Precharge Open AIR Indicate Error; Shutdown Circuit: GOOD; Shutdown Circuit: BAD; Precharge is Too Slow Too Fast

Precharge
Close Precharge
Open AIR
Measure TS voltage

TS voltage meets
target %
Correct timing

Default
(State value not found
in state machine)

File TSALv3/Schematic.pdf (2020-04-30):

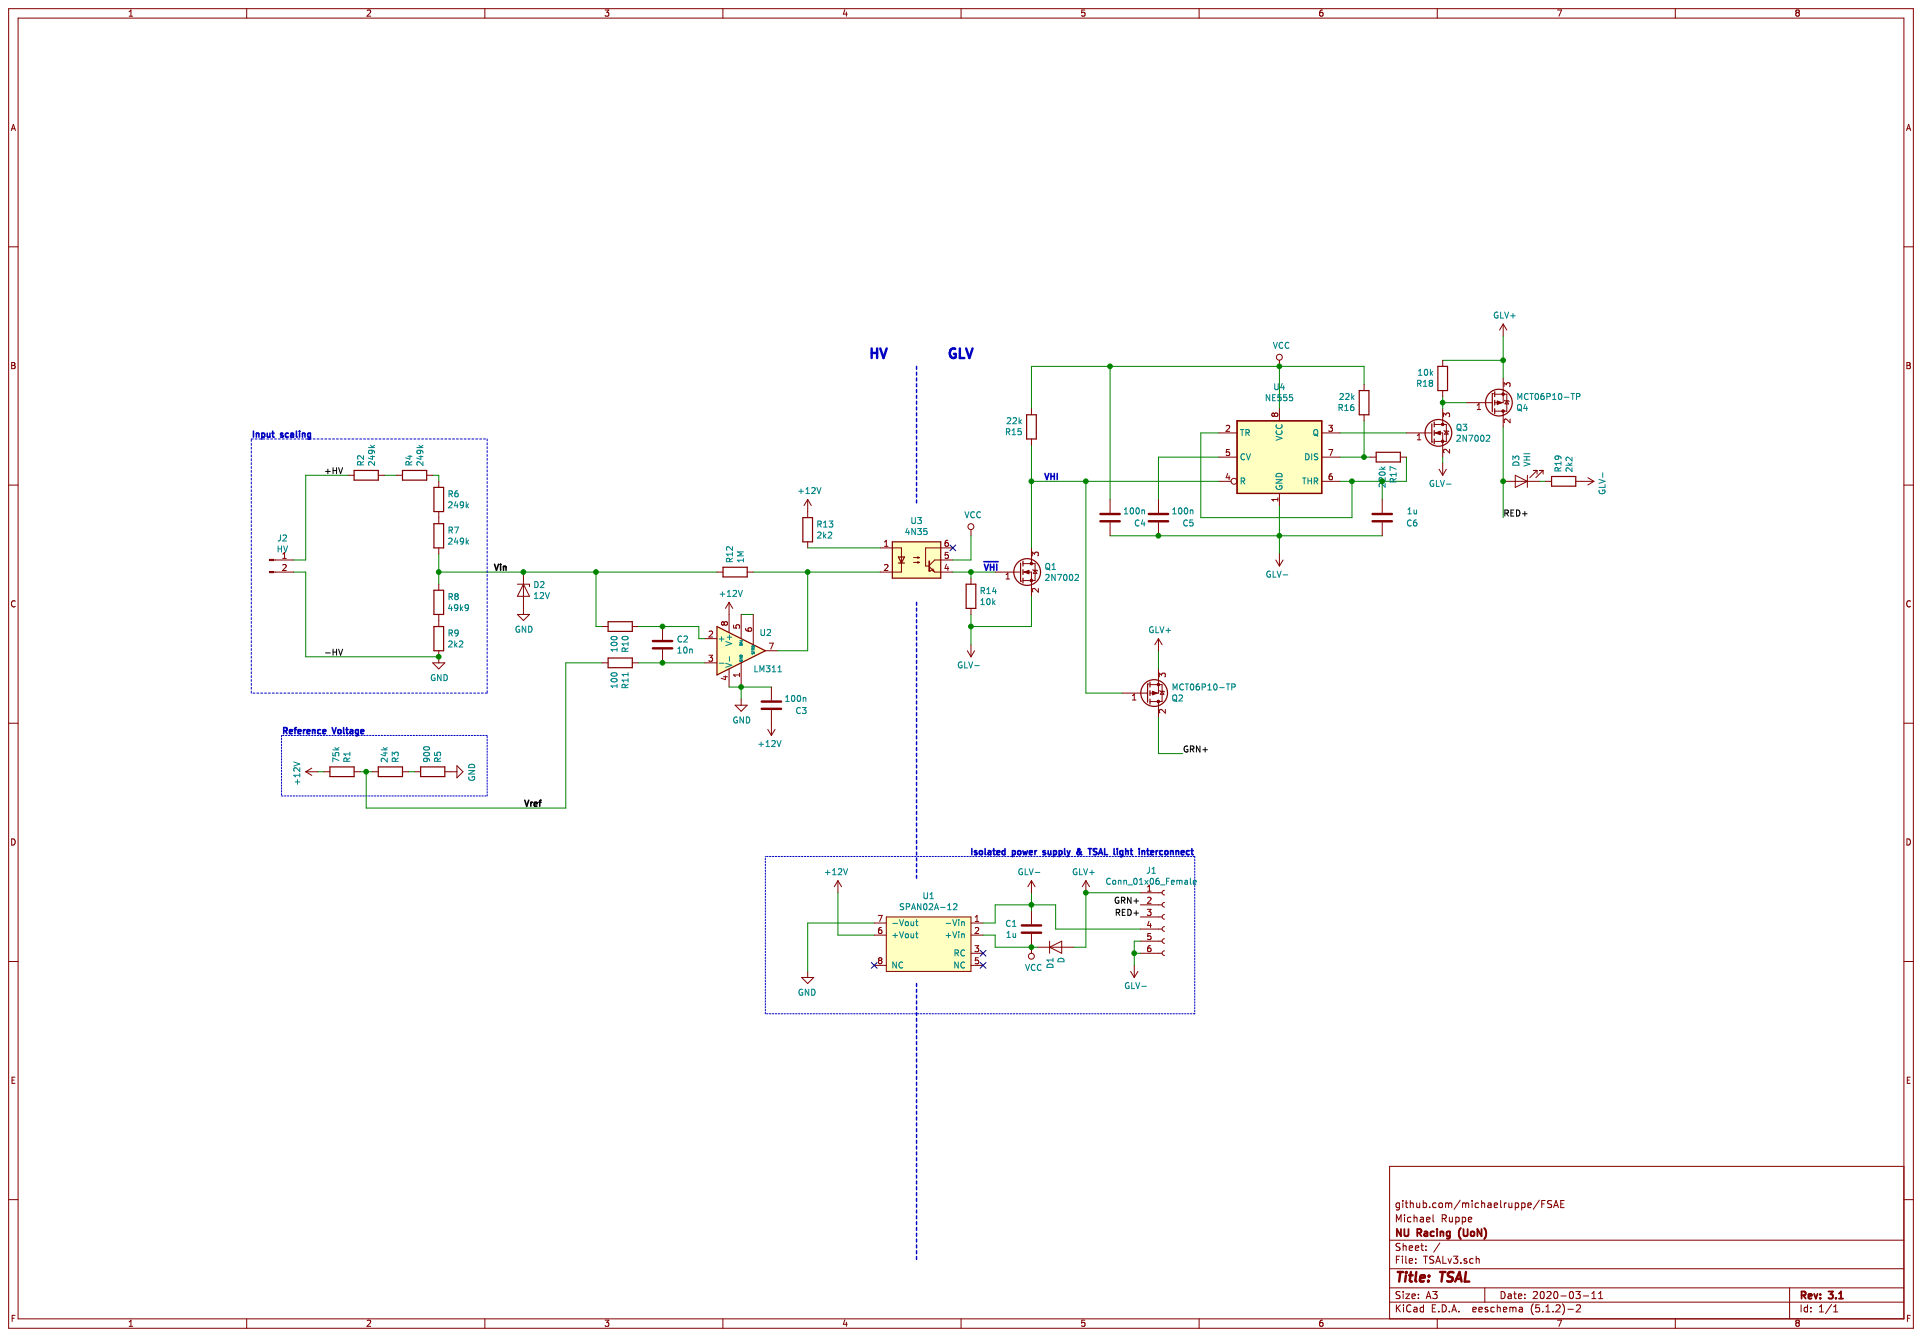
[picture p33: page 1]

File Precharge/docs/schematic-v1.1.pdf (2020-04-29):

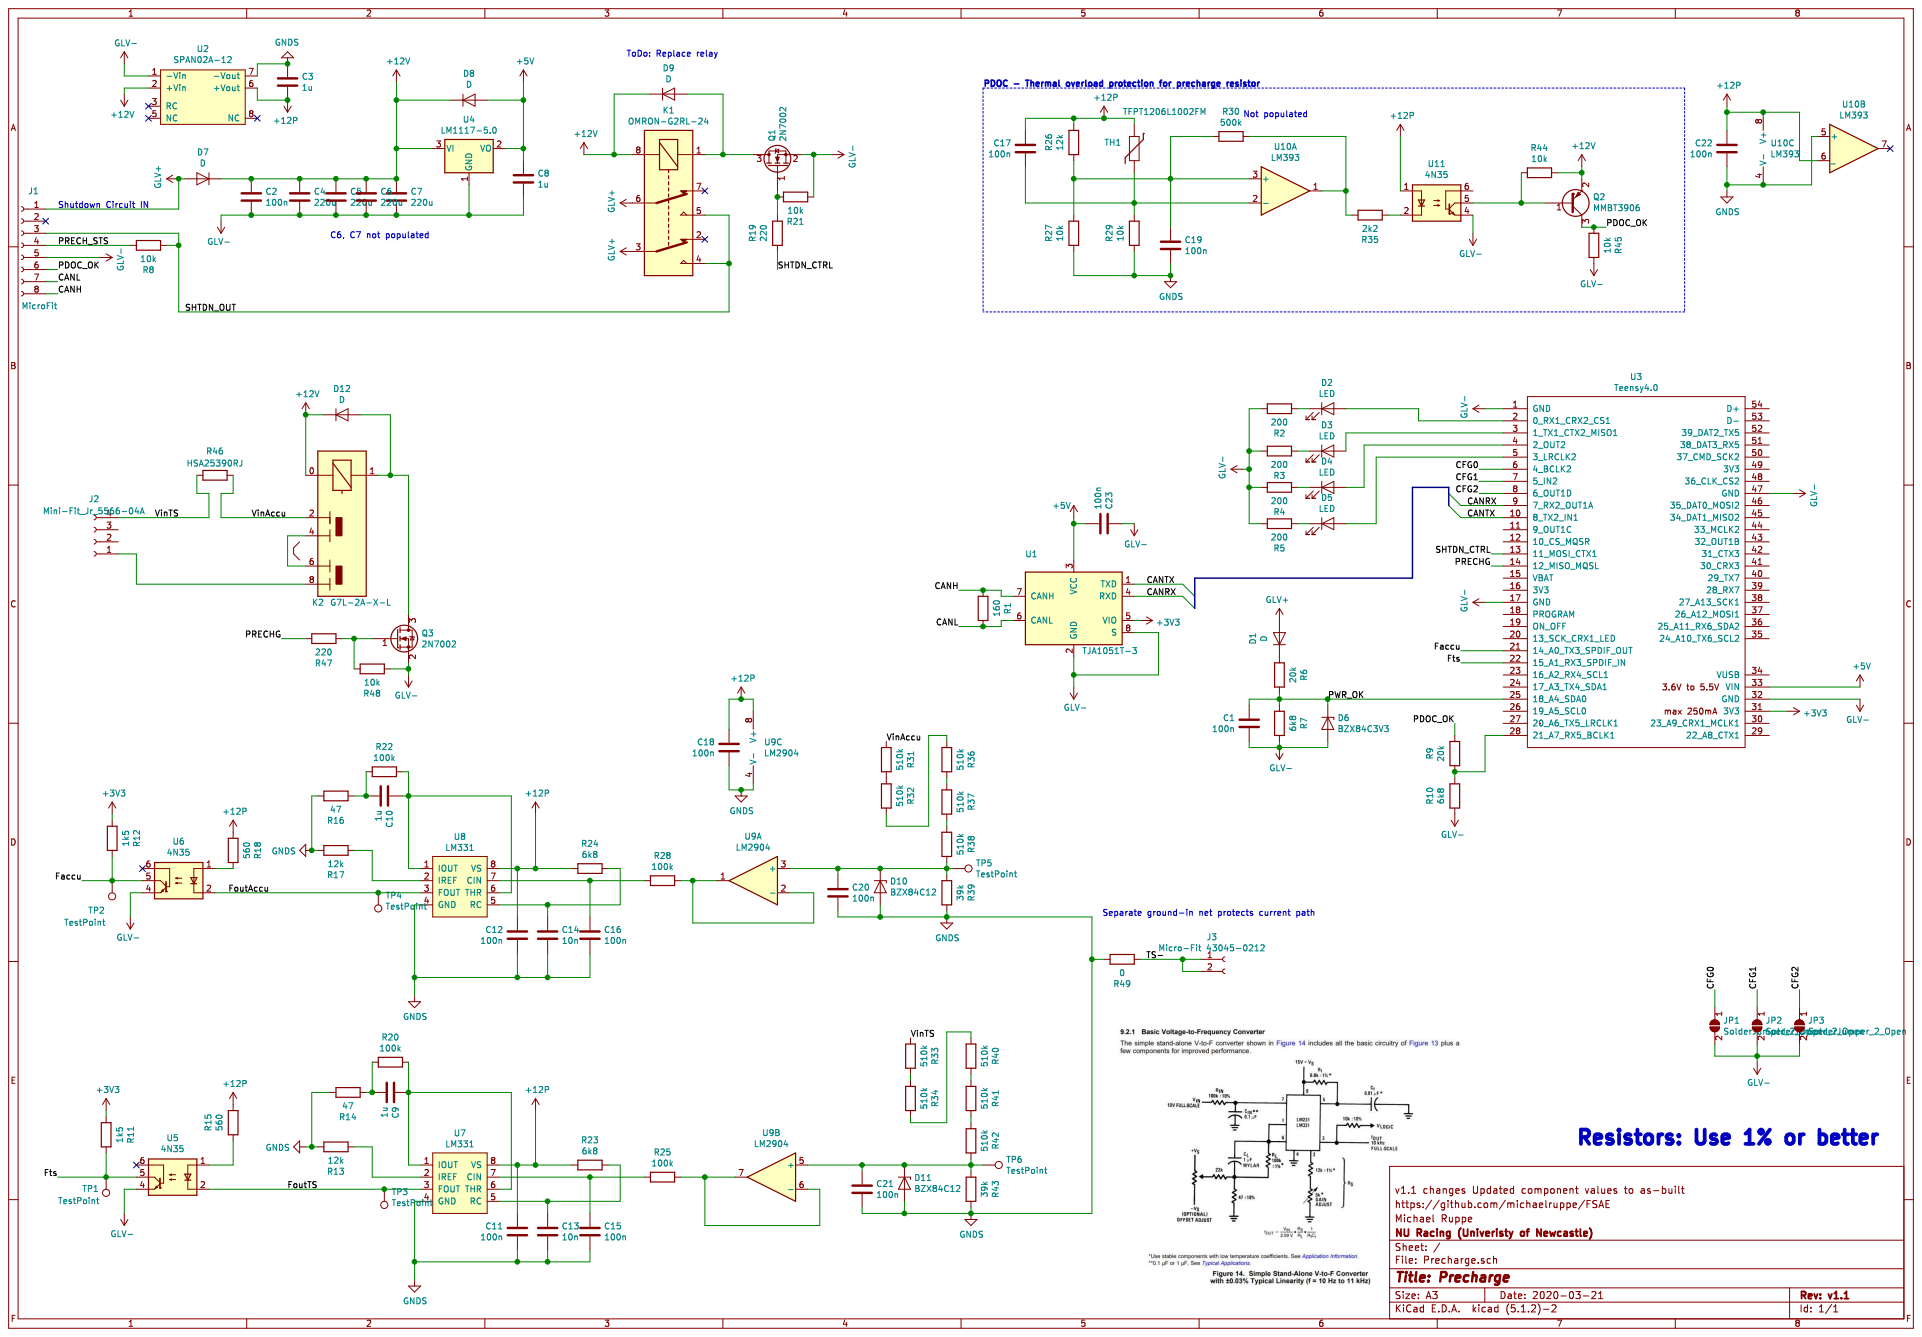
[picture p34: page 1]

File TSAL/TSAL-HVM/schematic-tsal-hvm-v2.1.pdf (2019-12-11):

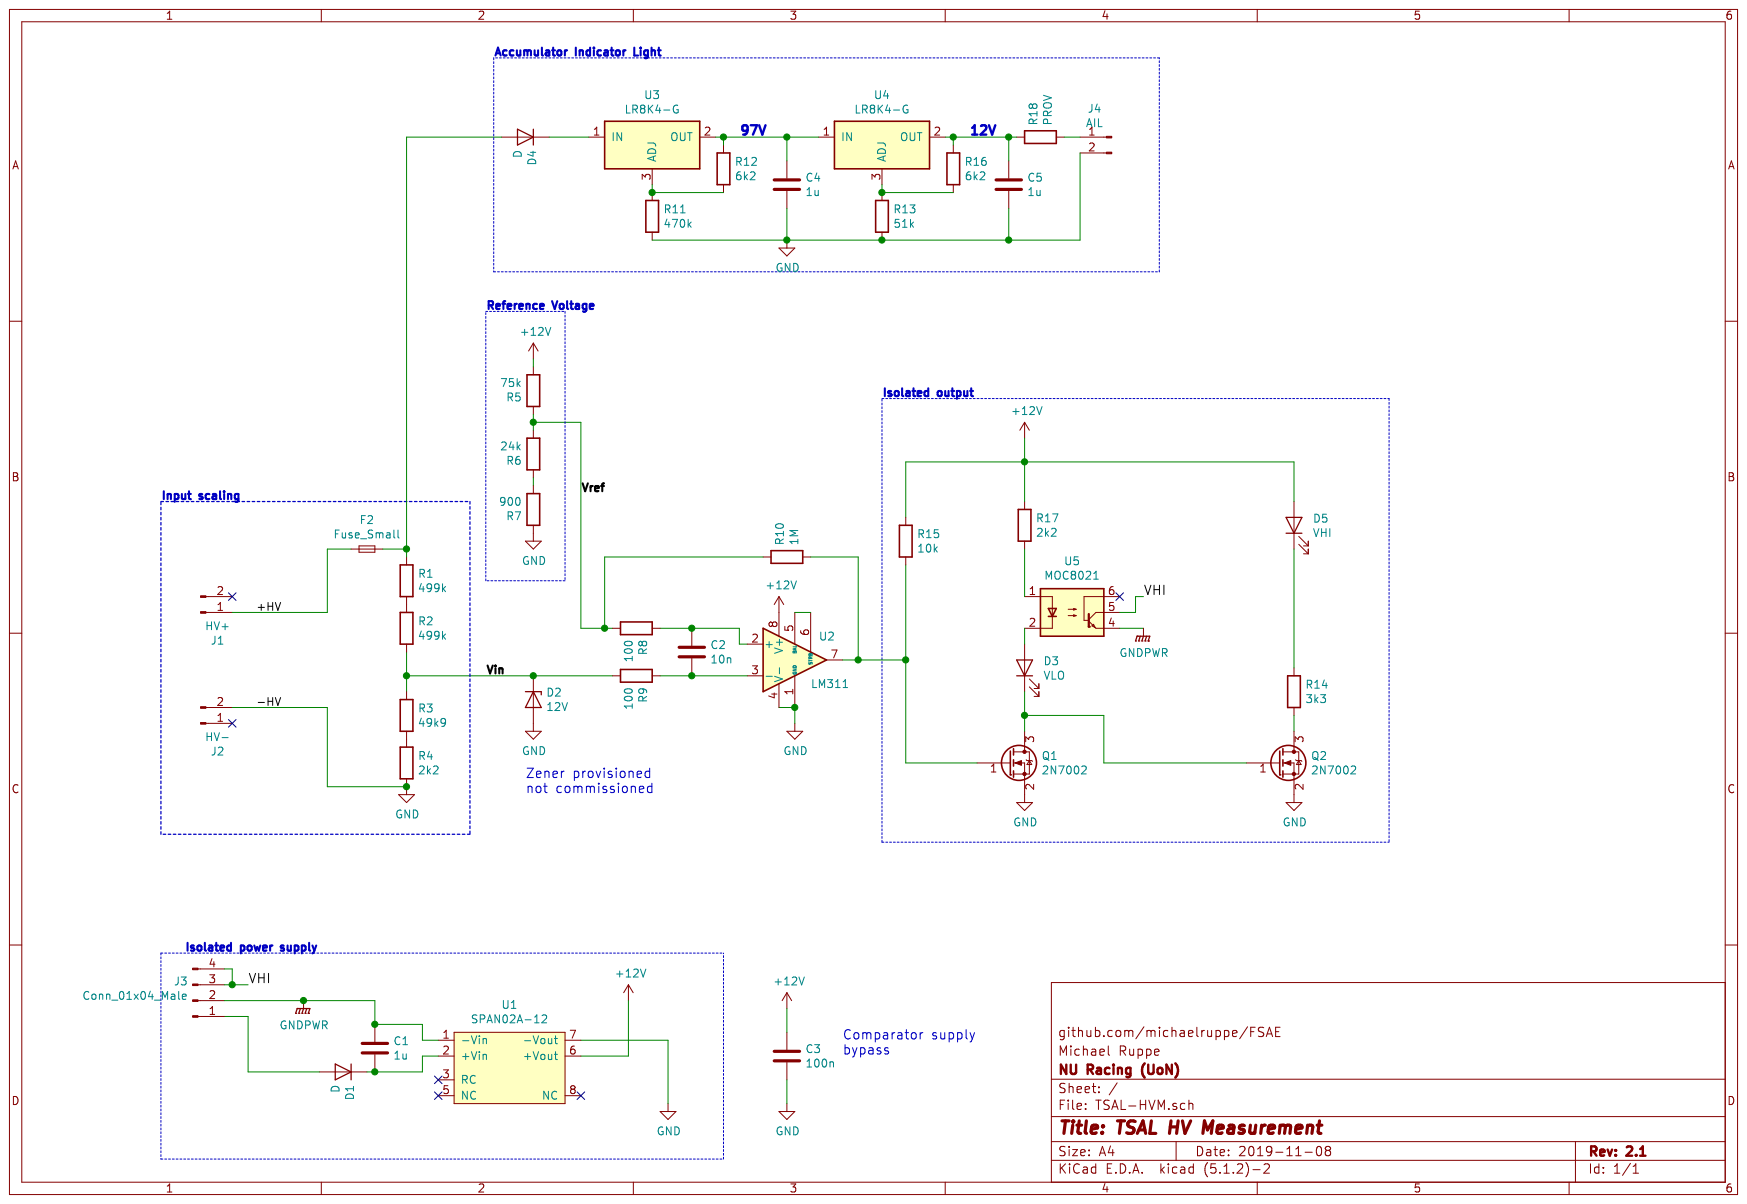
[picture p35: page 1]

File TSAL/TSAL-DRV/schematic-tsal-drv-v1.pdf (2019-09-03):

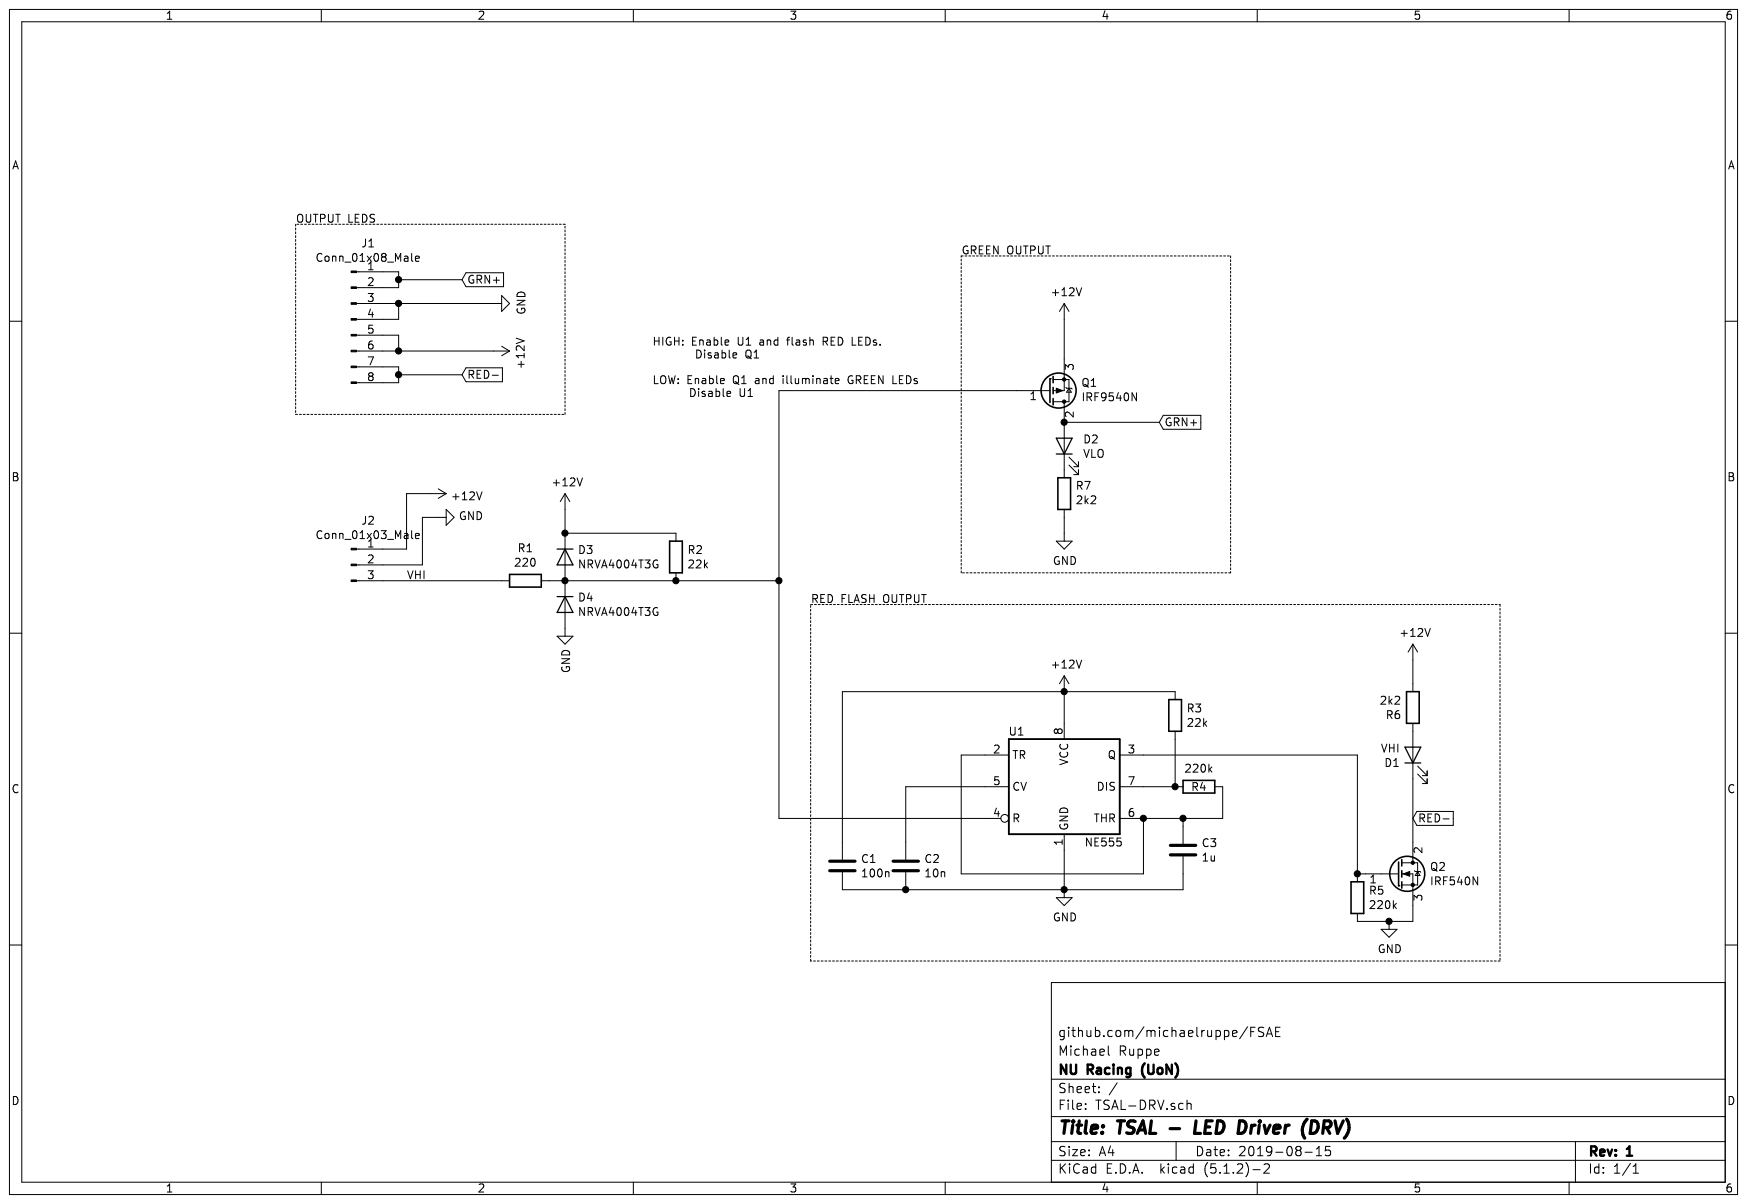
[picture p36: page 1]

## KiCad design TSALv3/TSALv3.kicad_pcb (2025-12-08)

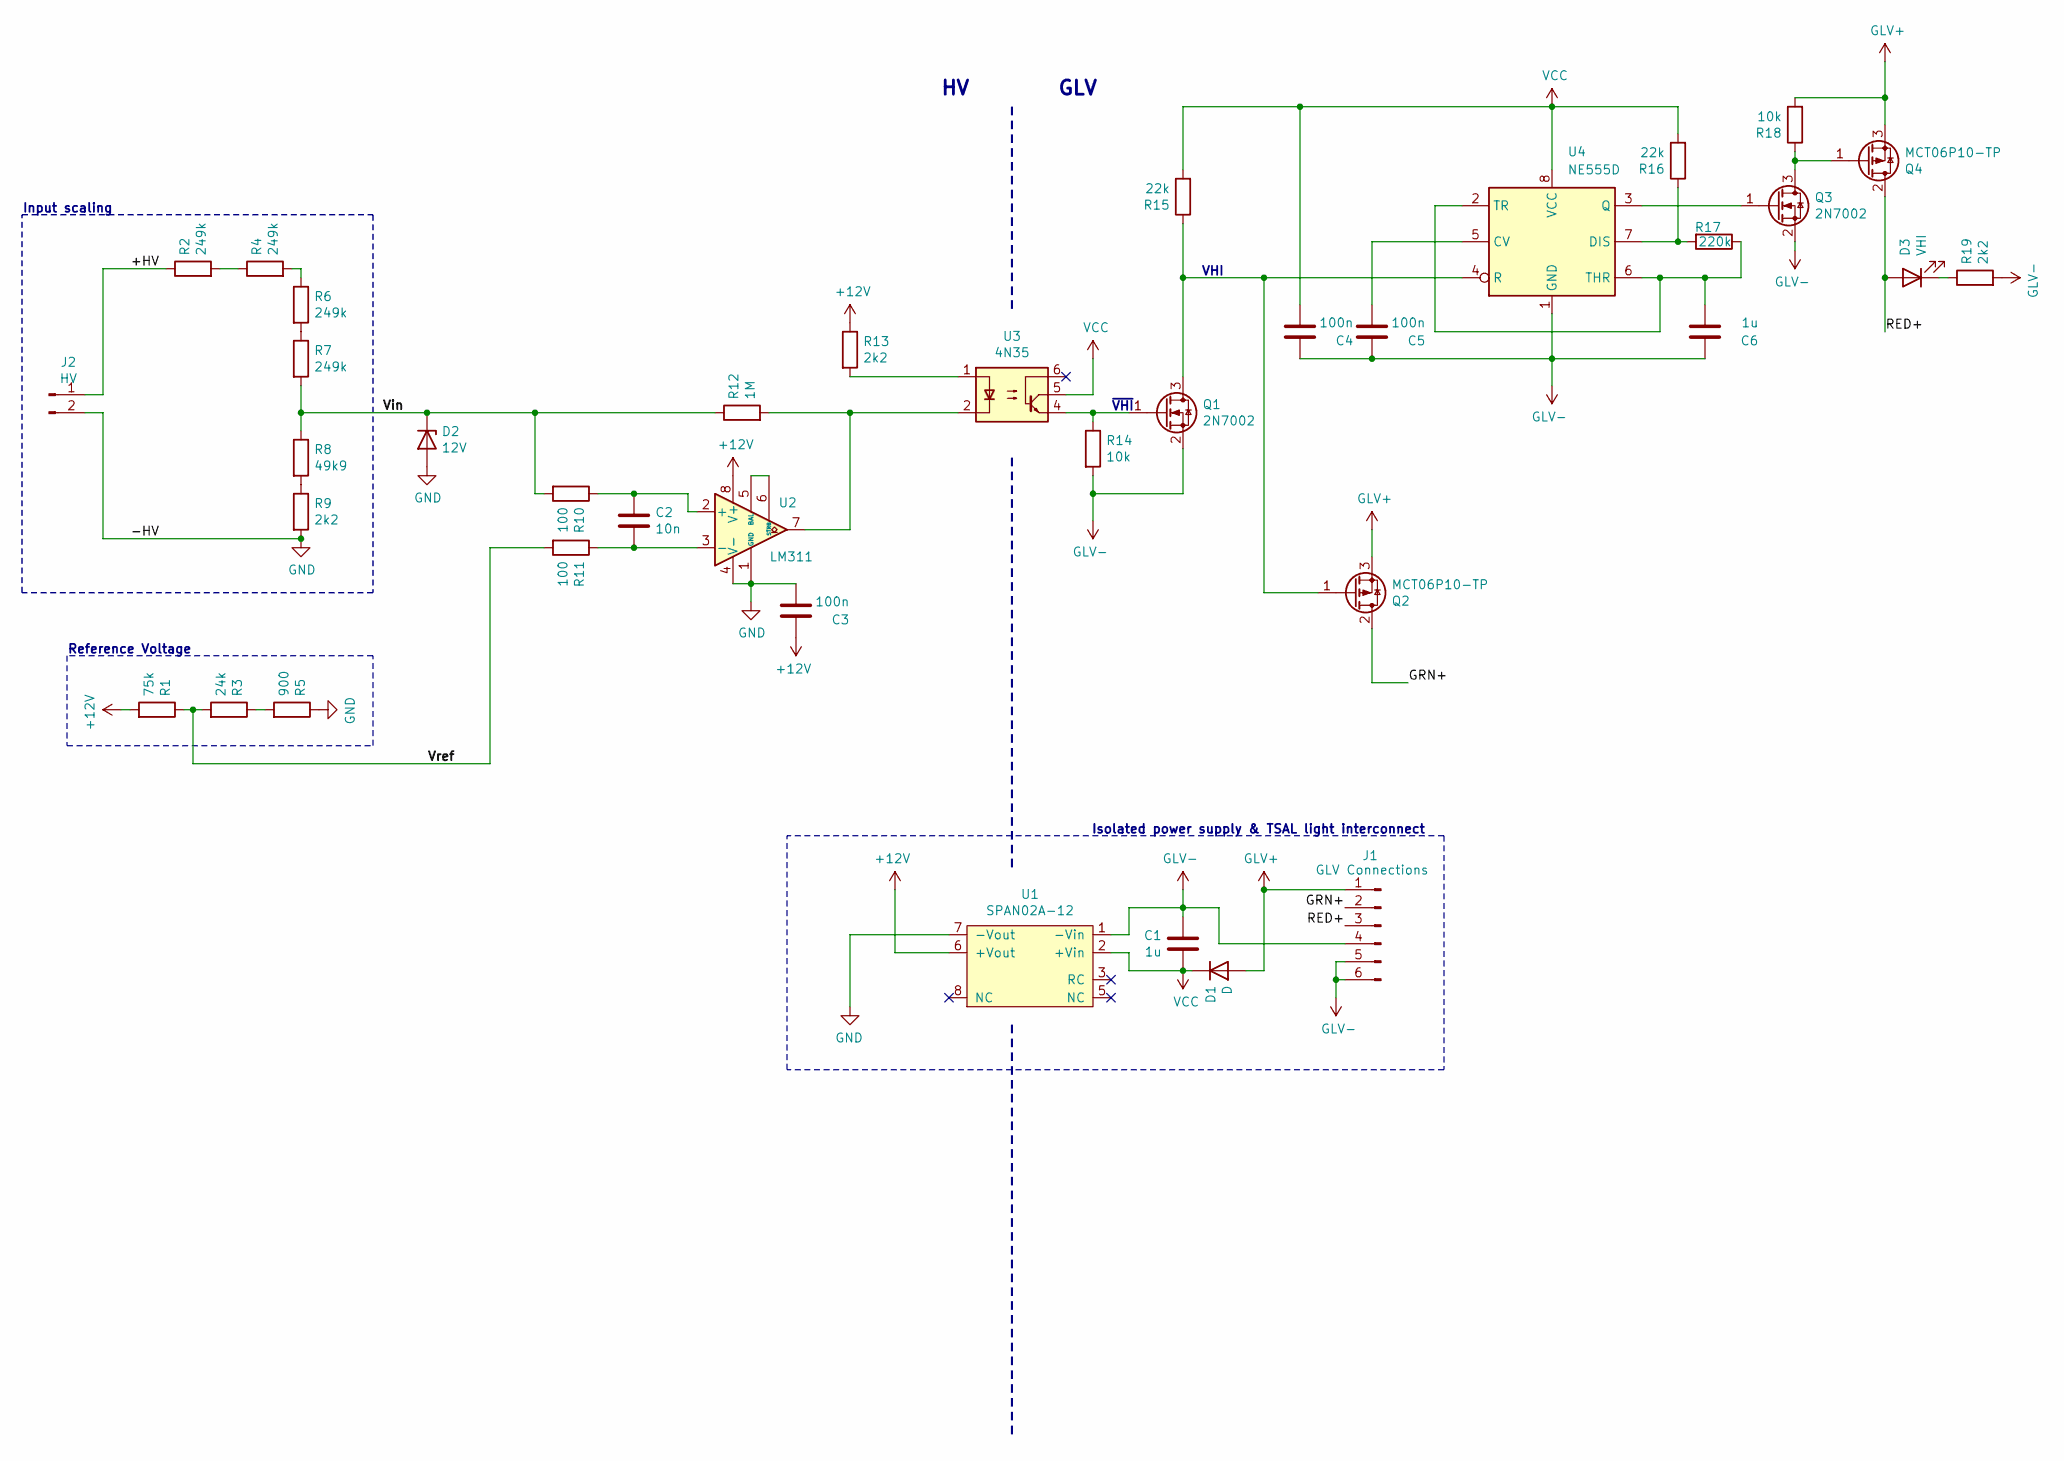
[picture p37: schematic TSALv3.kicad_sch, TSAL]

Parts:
C1, C6: 1u; C_0805_2012Metric_Pad1.15x1.40mm_HandSolder
C2: 10n; C_0805_2012Metric_Pad1.15x1.40mm_HandSolder
C3, C4, C5: 100n; C_0805_2012Metric_Pad1.15x1.40mm_HandSolder
D1: D; D_SMA
D2: 12V; D_DO-35_SOD27_P7.62mm_Horizontal
D3: VHI; LED_0805_2012Metric_Pad1.15x1.40mm_HandSolder
J1: GLV Connections; Molex_Micro-Fit_3.0_43045-0612_2x03_P3.00mm_Vertical
J2: HV; Molex_Mini-Fit_Jr_5566-02A_2x01_P4.20mm_Vertical
Q1, Q3: 2N7002; SOT-23
Q2, Q4: MCT06P10-TP; SOT-223-3_TabPin2
R1: 75k; R_1206_3216Metric_Pad1.42x1.75mm_HandSolder
R2, R4, R6, R7: 249k; R_1206_3216Metric_Pad1.42x1.75mm_HandSolder
R3: 24k; R_1206_3216Metric_Pad1.42x1.75mm_HandSolder
R5: 900; R_1206_3216Metric_Pad1.42x1.75mm_HandSolder
R8: 49k9; R_1206_3216Metric_Pad1.42x1.75mm_HandSolder
R9, R13, R19: 2k2; R_1206_3216Metric_Pad1.42x1.75mm_HandSolder
R10, R11: 100; R_1206_3216Metric_Pad1.42x1.75mm_HandSolder
R12: 1M; R_1206_3216Metric_Pad1.42x1.75mm_HandSolder
R14, R18: 10k; R_1206_3216Metric_Pad1.42x1.75mm_HandSolder
R15, R16: 22k; R_1206_3216Metric_Pad1.42x1.75mm_HandSolder
R17: 220k; R_1206_3216Metric_Pad1.42x1.75mm_HandSolder
U1: SPAN02A-12; SPAN02
U2: LM311; SOIC-8_3.9x4.9mm_P1.27mm
U3: 4N35; DIP-6_W7.62mm
U4: NE555D; SOIC-8_3.9x4.9mm_P1.27mm

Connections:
+12V: C3.1, R1.2, R13.1, U1.6 (+Vout), U2.8 (V+)
/+HV: J2.1, R2.1
/GRN+: J1.2, Q2.2 (D)
/RED+: D3.2 (A), J1.3, Q4.2 (D)
/Vin: D2.1 (K), R7.2, R8.1, R10.2, R12.1
/Vref: R1.1, R3.2, R11.2
GLV+: D1.2 (A), J1.1, Q2.3 (S), Q4.3 (S), R18.2
GLV-: C1.1, C4.1, C5.1, C6.1, J1.4, J1.5, J1.6, Q1.2 (S), Q3.2 (S), R14.2, R19.2, U1.1 (-Vin), U4.1 (GND)
GND: C3.2, D2.2 (A), J2.2, R5.1, R9.2, U1.7 (-Vout), U2.1 (GND), U2.4 (V-)
unnamed: C2.1, R10.1, U2.2 (+)
unnamed: C2.2, R11.1, U2.3 (-)
unnamed: C5.2, U4.5 (CV)
unnamed: C6.2, R17.1, U4.2 (TR), U4.6 (THR)
unnamed: D3.1 (K), R19.1
unnamed: Q1.1 (G), R14.1, U3.4
unnamed: Q1.3 (D), Q2.1 (G), R15.1, U4.4 (R)
unnamed: Q3.1 (G), U4.3 (Q)
unnamed: Q3.3 (D), Q4.1 (G), R18.1
unnamed: R2.2, R4.1
unnamed: R3.1, R5.2
unnamed: R4.2, R6.1
unnamed: R6.2, R7.1
unnamed: R8.2, R9.1
unnamed: R12.2, U2.7, U3.2
unnamed: R13.2, U3.1
unnamed: R16.1, R17.2, U4.7 (DIS)
unnamed: U2.5 (BAL), U2.6 (STRB)
VCC: C1.2, C4.2, D1.1 (K), R15.2, R16.2, U1.2 (+Vin), U3.5, U4.8 (VCC)

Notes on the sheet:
VHI
Isolated power supply & TSAL light interconnect
Reference Voltage
GLV
~{VHI}
Input scaling

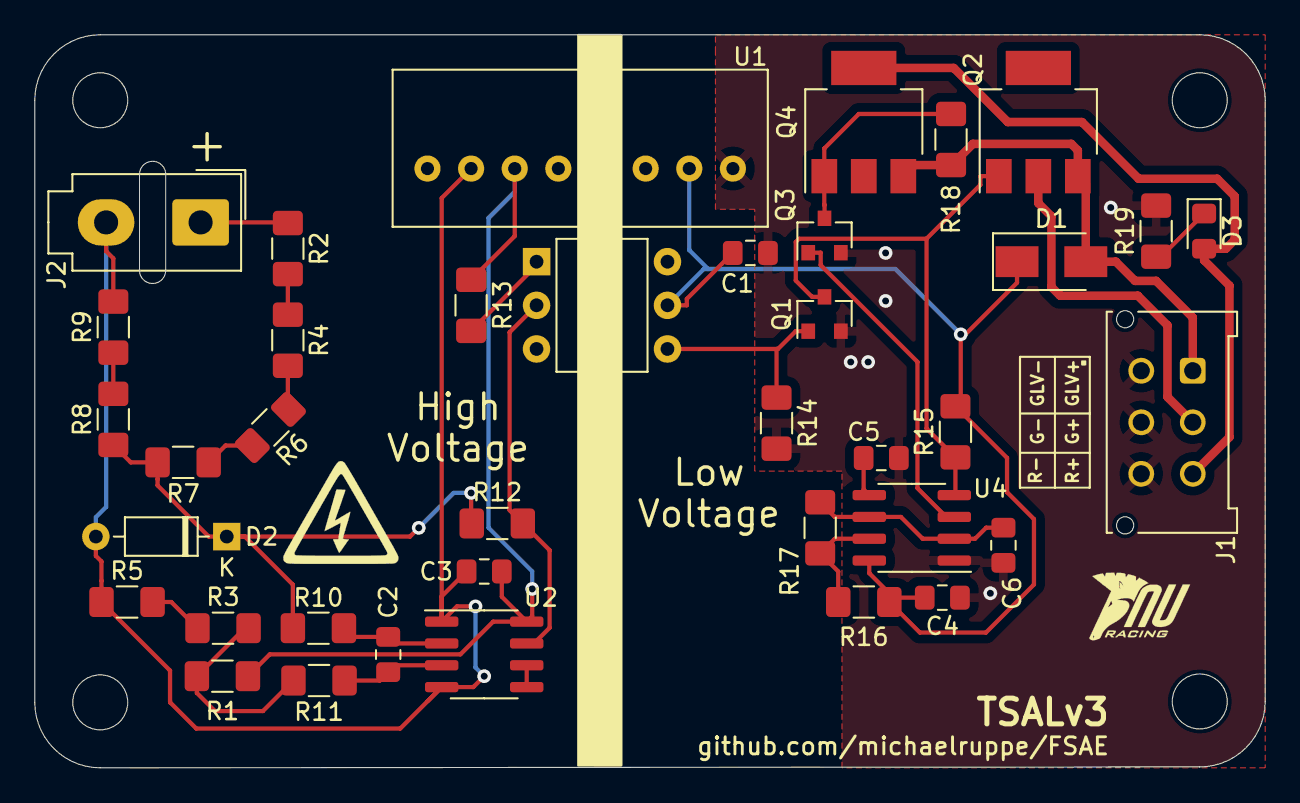
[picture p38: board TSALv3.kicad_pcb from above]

Board: 2 copper layers, 71.6 x 42.7 mm, 42 parts (0 on the bottom side), 28 nets.

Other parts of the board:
MH1, MH2, MH3, MH4: MountingHole_3.2mm_M3

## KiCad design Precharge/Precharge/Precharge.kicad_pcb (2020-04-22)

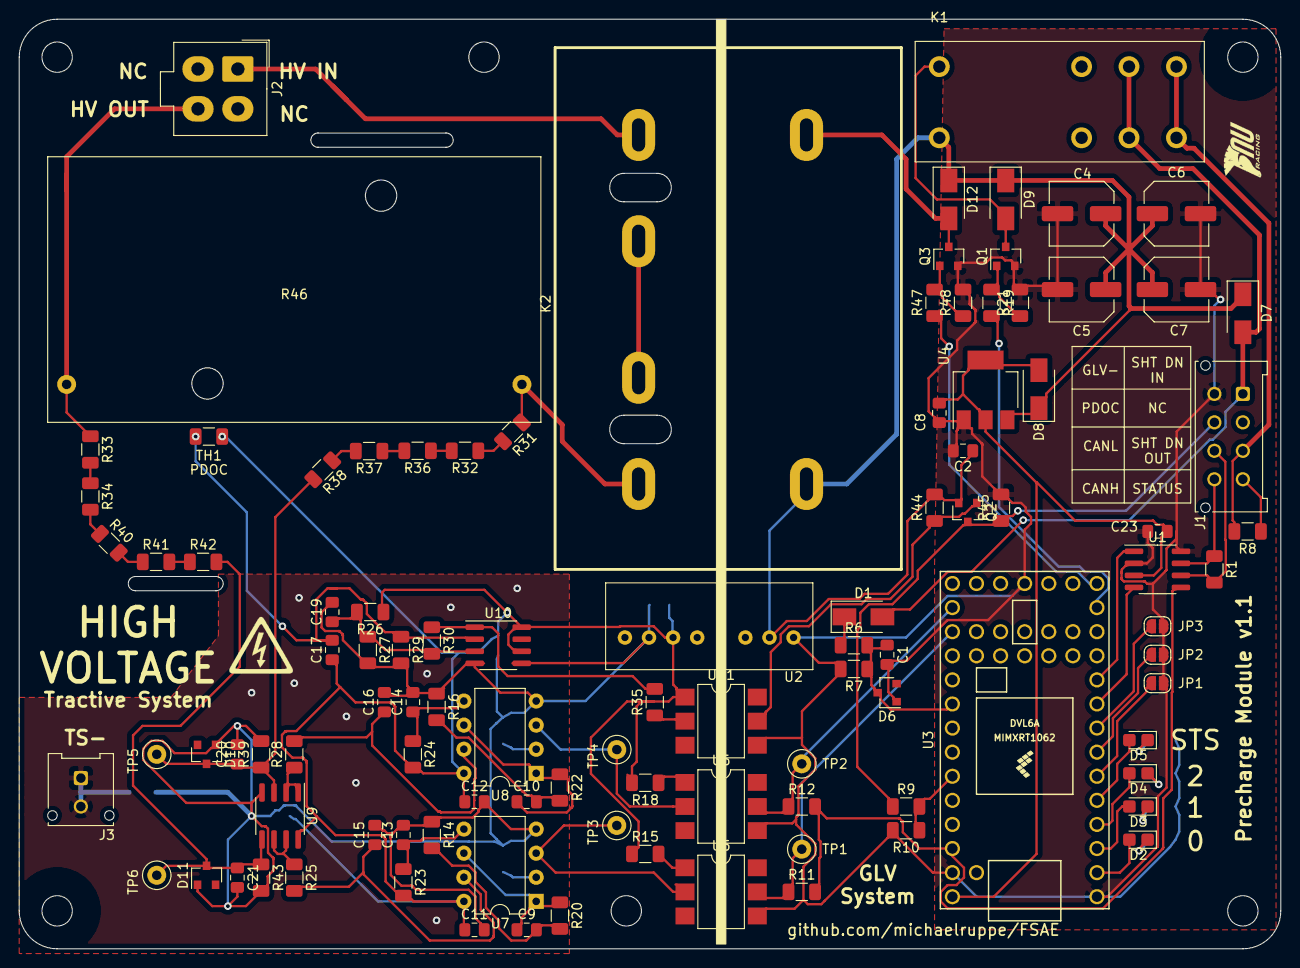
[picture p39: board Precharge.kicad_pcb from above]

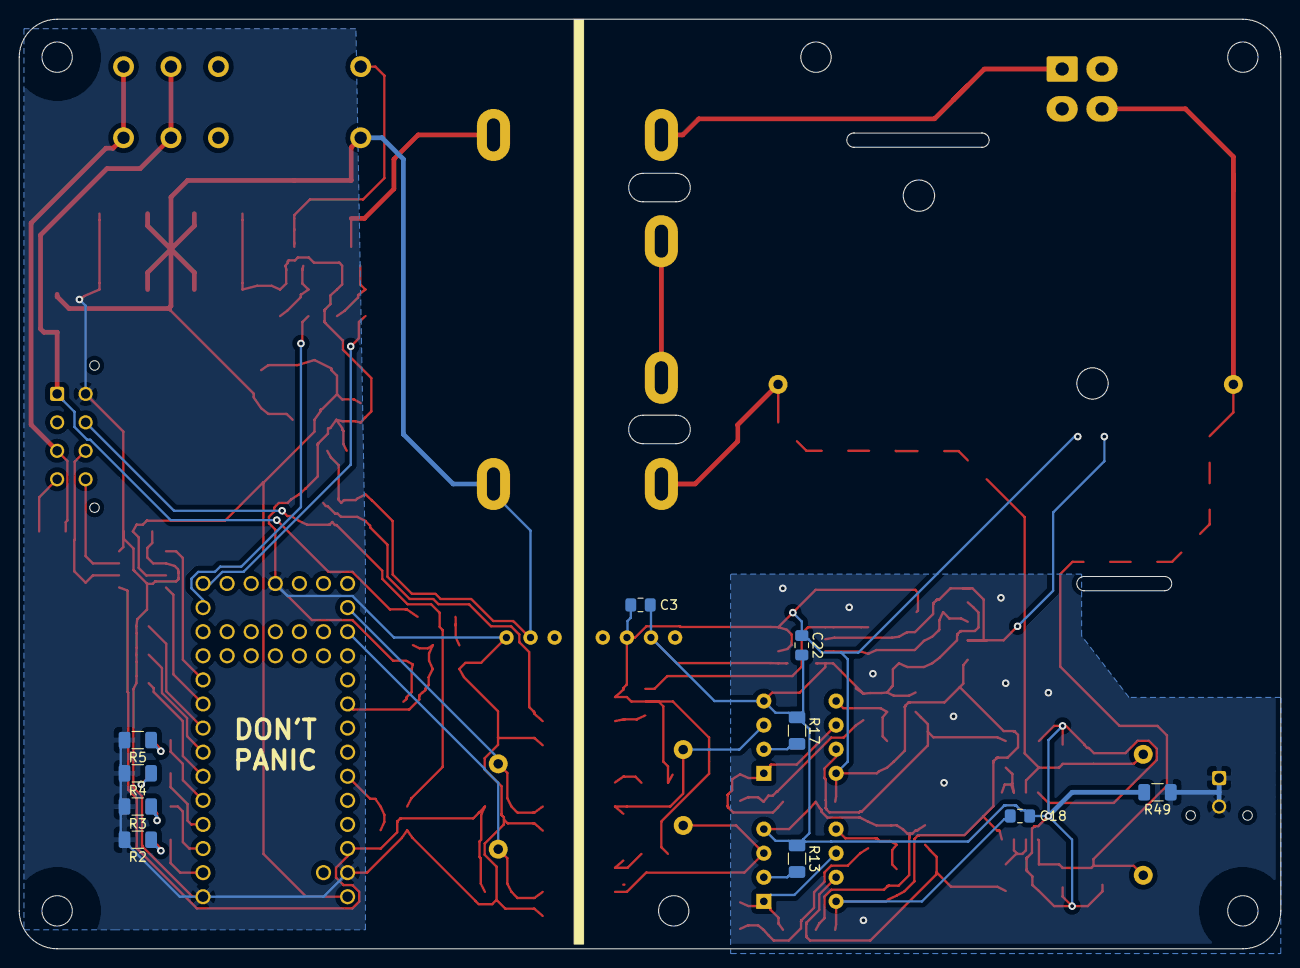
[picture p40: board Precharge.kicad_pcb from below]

Board: 2 copper layers, 133.0 x 98.0 mm, 119 parts (10 on the bottom side), 72 nets.

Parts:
C1, C2, C11, C12, C15, C16, C17, C18, C19, C20, C21, C22, C23: 100n; C_0805_2012Metric_Pad1.15x1.40mm_HandSolder
C3, C8, C9, C10: 1u; C_0805_2012Metric_Pad1.15x1.40mm_HandSolder
C4, C5, C6, C7: 220u; C_Elec_6.3x5.4
C13, C14: 10n; C_0805_2012Metric_Pad1.15x1.40mm_HandSolder
D1, D7, D8, D9, D12: D; D_SMA
D2, D3, D4, D5: LED; LED_0805_2012Metric_Castellated
D6: BZX84C3V3; D_SOT-23_ANK
D10, D11: BZX84C12; D_SOT-23_ANK
J1: MicroFit; Molex_Micro-Fit_3.0_43045-0812_2x04_P3.00mm_Vertical
J2: Mini-Fit_Jr_5566-04A; Molex-Mini-Fit-Jr-4-pin-P4.2mm-RowP4.2mm
J3: Micro-Fit 43045-0212; Molex_Micro-Fit_3.0_43045-0212_2x01_P3.00mm_Vertical
JP1, JP2, JP3: SolderJumper_2_Open; SolderJumper-2_P1.3mm_Open_RoundedPad1.0x1.5mm
K1: OMRON-G2RL-24; OMRON-G2R-24
K2: G7L-2A-X-L
MT1, MT2, MT3, MT4, MT5, MT6: MountingHole_3.2mm_M3
Q1, Q3: 2N7002; SOT-23
Q2: MMBT3906; SOT-23
R1: 160; R_1206_3216Metric
R2, R3, R4, R5: 200; R_1206_3216Metric
R6, R9: 20k; R_1206_3216Metric
R7, R10, R23, R24: 6k8; R_1206_3216Metric
R8, R21, R26, R27, R29, R44, R45, R48: 10k; R_1206_3216Metric
R11, R12: 1k5; R_1206_3216Metric
R13, R17: 12k; R_1206_3216Metric
R14, R16: 47; R_1206_3216Metric
R15, R18: 560; R_1206_3216Metric
R19, R47: 220; R_1206_3216Metric
R20, R22, R25, R28: 100k; R_1206_3216Metric
R30: 500k; R_1206_3216Metric
R31, R32, R33, R34, R36, R37, R38, R40, R41, R42: 510k; R_1206_3216Metric
R35: 2k2; R_1206_3216Metric
R39, R43: 39k; R_1206_3216Metric
R46: HSA25390RJ; Chassis_Resistor_TE_Connectivity_HSA25
R49: 0; R_1206_3216Metric
TH1: TFPT1206L1002FM; R_1206_3216Metric
TP1, TP2, TP3, TP4, TP5, TP6: TestPoint; TestPoint_Loop_D2.50mm_Drill1.0mm_LowProfile
U1: TJA1051T-3; SOIC-8_3.9x4.9mm_P1.27mm
U2: SPAN02A-12; SPAN02
U3: Teensy4.0; Teensy40
U4: LM1117-5.0; SOT-223-3_TabPin2
U5, U6, U11: 4N35; SMDIP-6_W7.62mm
U7, U8: LM331; DIP-8_W7.62mm
U9: LM2904; SOIC-8_3.9x4.9mm_P1.27mm
U10: LM393; SOIC-8_3.9x4.9mm_P1.27mm

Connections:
+3V3: R11.2, R12.2, U1.5, U3.31
+5V: C8.1, C23.2, D8.2, U1.3, U3.33, U4.2
+12P: C3.2, C11.1, C12.1, C17.1, C18.1, C22.1, R15.1, R18.2, R23.2, R24.2, R26.1, TH1.2, U2.6, U7.8, U8.8, U9.8, U10.6, U10.8, U11.1
+12V: C2.1, C4.1, C5.1, C6.1, C7.1, D7.1, D8.1, D9.1, D12.1, K1.8, K2.0, Q2.2, R44.2, U2.2, U4.3
/CANH: J1.8, R1.1, U1.7
/CANL: J1.7, R1.2, U1.6
/CANRX: U1.4, U3.9
/CANTX: U1.1, U3.10
/CFG0: JP1.1, U3.6
/CFG1: JP2.1, U3.7
/CFG2: JP3.1, U3.8
/Faccu: R12.1, TP2.1, U3.21, U6.5
/FoutAccu: TP4.1, U6.2, U8.3
/FoutTS: TP3.1, U5.2, U7.3
/Fts: R11.1, TP1.1, U3.22, U5.5
/PDOC_OK: J1.6, Q2.3, R9.1, R45.1
/PRECHG: R47.1, U3.14
/PRECH_STS: J1.4, R8.1
/PWR_OK: C1.1, D6.1, R6.2, R7.1, U3.25
/SHTDN_CTRL: R19.2, U3.13
/SHTDN_OUT: J1.3, K1.4, K1.5, R8.2
/TS-: J3.1, J3.2, R49.1
/VinAccu: K2.2, R31.1, R46.1
/VinTS: J2.4, R33.1, R46.2
GLV+: D1.2, D7.2, J1.1, K1.3, K1.6
GLV-: C1.2, C2.2, C4.2, C5.2, C6.2, C7.2, C8.2, C23.1, D6.2, J1.5, JP1.2, JP2.2, JP3.2, Q1.2, Q3.2, R2.2, R3.2, R4.2, R5.2, R7.2, R10.2, R21.2, R45.2, R48.2, U1.2, U1.8, U2.1, U3.1, U3.17, U3.32, U4.1, U5.4, U6.4, U11.4
GNDS: C3.1, C11.2, C12.2, C13.2, C14.2, C15.2, C16.2, C18.2, C19.2, C20.2, C21.2, C22.2, D10.2, D11.2, R13.1, R14.1, R16.1, R17.1, R27.2, R29.2, R39.2, R43.2, R49.2, U2.7, U7.4, U8.4, U9.4, U10.4, U10.5
unnamed: C9.1, R20.1, U7.1, U7.6
unnamed: C9.2, R14.2, R20.2
unnamed: C10.1, R22.1, U8.1, U8.6
unnamed: C10.2, R16.2, R22.2
unnamed: C13.1, R23.1, U7.5
unnamed: C14.1, R24.1, U8.5
unnamed: C15.1, R25.2, U7.7
unnamed: C16.1, R28.2, U8.7
unnamed: C17.2, R29.1, TH1.1, U10.2
unnamed: C19.1, R26.2, R27.1, R30.2, U10.3
unnamed: C20.1, D10.1, R38.2, R39.1, TP5.1, U9.3
unnamed: C21.1, D11.1, R42.2, R43.1, TP6.1, U9.5
unnamed: D1.1, R6.1
unnamed: D2.1, R2.1
unnamed: D2.2, U3.2
unnamed: D3.1, R3.1
unnamed: D3.2, U3.3
unnamed: D4.1, R4.1
unnamed: D4.2, U3.4
unnamed: D5.1, R5.1
unnamed: D5.2, U3.5
unnamed: D9.2, K1.1, Q1.3
unnamed: D12.2, K2.1, Q3.3
unnamed: J2.1, K2.8
unnamed: K2.4, K2.6
unnamed: Q1.1, R19.1, R21.1
unnamed: Q2.1, R44.1, U11.5
unnamed: Q3.1, R47.2, R48.1
unnamed: R9.2, R10.1, U3.28
unnamed: R13.2, U7.2
unnamed: R15.2, U5.1
unnamed: R17.2, U8.2
unnamed: R18.1, U6.1
unnamed: R25.1, U9.6, U9.7
unnamed: R28.1, U9.1, U9.2
unnamed: R30.1, R35.2, U10.1
unnamed: R31.2, R32.1
unnamed: R32.2, R36.1
unnamed: R33.2, R34.1
unnamed: R34.2, R40.1
unnamed: R35.1, U11.2
unnamed: R36.2, R37.1
unnamed: R37.2, R38.1
unnamed: R40.2, R41.1
unnamed: R41.2, R42.1

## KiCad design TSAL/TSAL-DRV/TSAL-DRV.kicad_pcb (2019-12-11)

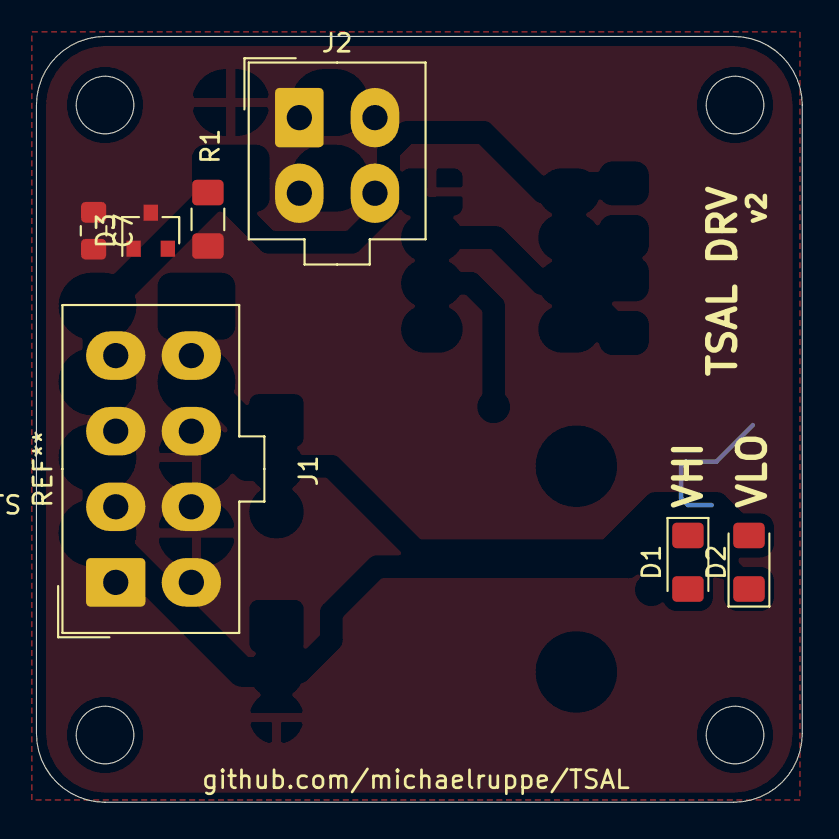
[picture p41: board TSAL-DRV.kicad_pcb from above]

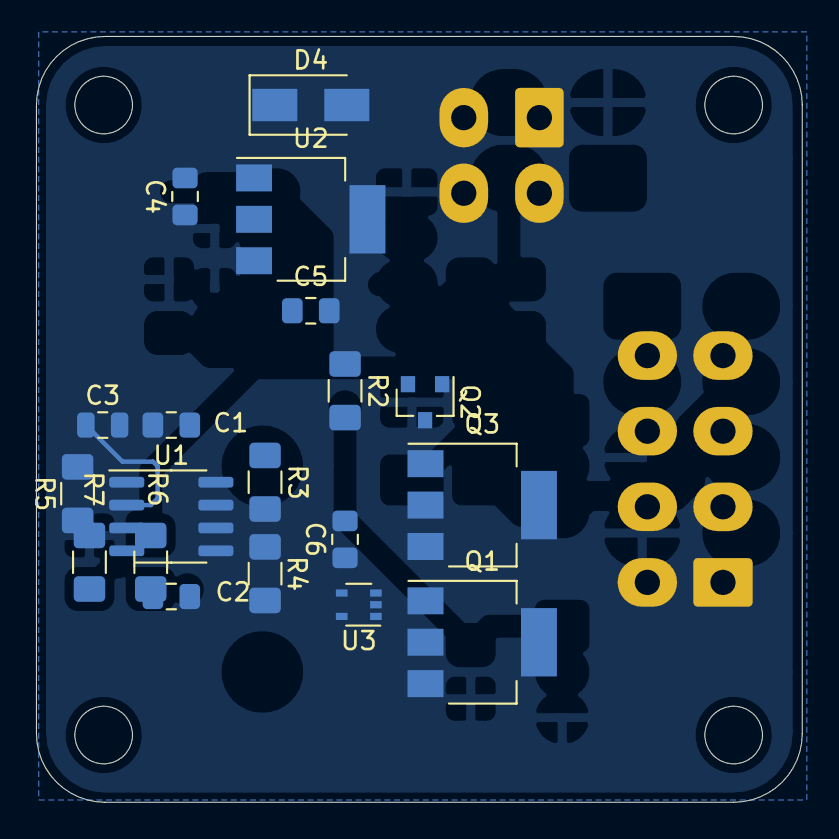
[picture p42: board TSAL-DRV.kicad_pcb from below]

Board: 2 copper layers, 42.5 x 42.5 mm, 26 parts (19 on the bottom side), 16 nets.

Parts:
C1, C6: 100n; C_0805_2012Metric_Pad1.15x1.40mm_HandSolder
C2, C7: 10n; C_0805_2012Metric_Pad1.15x1.40mm_HandSolder
C3: 1u; C_0805_2012Metric
C4, C5: 1u; C_0805_2012Metric_Pad1.15x1.40mm_HandSolder
D1: VHI; LED_1206_3216Metric_Pad1.42x1.75mm_HandSolder
D2: VLO; LED_1206_3216Metric_Pad1.42x1.75mm_HandSolder
D3: BZX84C5V1; D_SOT-23_ANK
D4: D; D_SMA
J1: Conn_01x08_Male; Molex-Mini-Fit-Jr-8-pin-P4.2mm-RowP4.2mm
J2: Conn_01x03_Male; Molex-Mini-Fit-Jr-4-pin-P4.2mm-RowP4.2mm
Q1, Q3: MCT06P10-TP; SOT-223-3_TabPin2
Q2: 2N7002; SOT-23
R1, R6, R7: 2k2; R_1206_3216Metric_Pad1.42x1.75mm_HandSolder
R2, R4, R5: 220k; R_1206_3216Metric_Pad1.42x1.75mm_HandSolder
R3: 22k; R_1206_3216Metric_Pad1.42x1.75mm_HandSolder
U1: NE555; SOIC-8_3.9x4.9mm_P1.27mm
U2: AMS1117-5.0; SOT-223-3_TabPin2
U3: 74LVC1G17; SOT-353_SC-70-5

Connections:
+5V: C1.1, C5.1, C6.1, R2.1, R3.1, U1.8, U2.2, U3.5
+12V: D4.2, J2.1, Q1.3, Q3.3
/VHI: J2.3, R1.2
GND: C1.2, C2.2, C3.2, C4.2, C5.2, C6.2, C7.2, D1.1, D3.2, J1.3, J1.4, J1.7, J1.8, J2.2, Q2.2, R5.2, R7.1, U1.1, U2.1, U3.3
GRN+: D2.2, J1.1, J1.2, Q1.2
unnamed: C2.1, U1.5
unnamed: C3.1, R4.1, U1.2, U1.6
unnamed: C4.1, D4.1, U2.3
unnamed: C7.1, D3.1, R1.1, U3.2
unnamed: D1.2, R6.2
unnamed: D2.1, R7.2
unnamed: Q1.1, U1.4, U3.4
unnamed: Q2.1, R5.1, U1.3
unnamed: Q2.3, Q3.1, R2.2
unnamed: R3.2, R4.2, U1.7
RED+: J1.5, J1.6, Q3.2, R6.1

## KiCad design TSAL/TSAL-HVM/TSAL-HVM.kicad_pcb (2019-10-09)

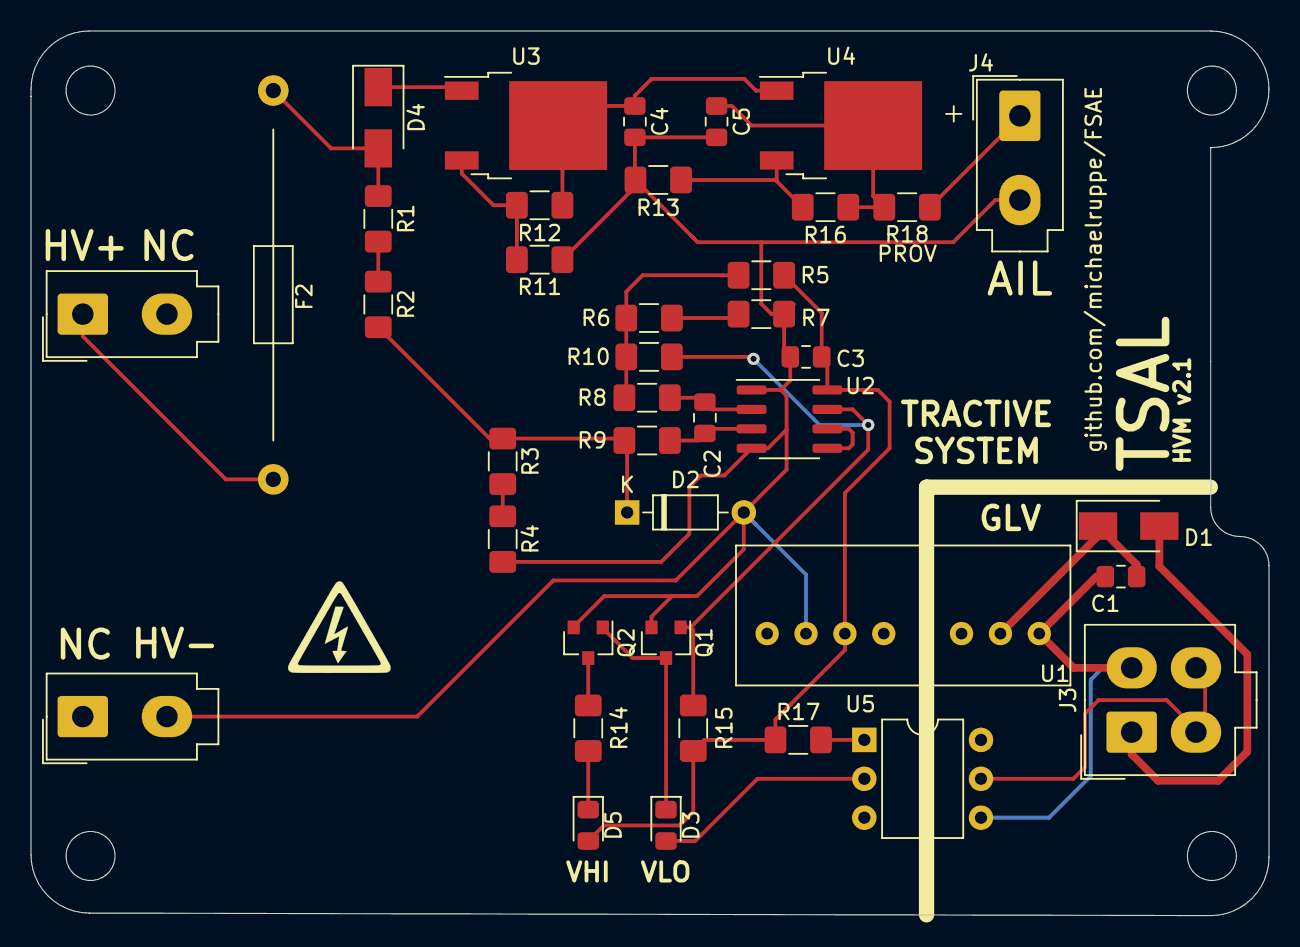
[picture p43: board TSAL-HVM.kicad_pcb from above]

Board: 2 copper layers, 80.9 x 57.8 mm, 40 parts (0 on the bottom side), 28 nets.

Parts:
C1, C4, C5: 1u; C_0805_2012Metric_Pad1.15x1.40mm_HandSolder
C2: 10n; C_0805_2012Metric_Pad1.15x1.40mm_HandSolder
C3: 100n; C_0805_2012Metric_Pad1.15x1.40mm_HandSolder
D1, D4: D; D_SMA
D2: 12V; D_DO-35_SOD27_P7.62mm_Horizontal
D3: VLO; LED_0805_2012Metric_Pad1.15x1.40mm_HandSolder
D5: VHI; LED_0805_2012Metric_Pad1.15x1.40mm_HandSolder
F2: Fuse_Small; BELFUSE-5HF
J1: HV+; Molex_Mini-Fit_Jr_5566-02A_2x01_P4.20mm_Vertical
J2: HV-; Molex_Mini-Fit_Jr_5566-02A_2x01_P4.20mm_Vertical
J3: Conn_01x04_Male; Molex-Mini-Fit-Jr-4-pin-P4.2mm-RowP4.2mm
J4: AIL; Molex_Mini-Fit_Jr_5566-02A_2x01_P4.20mm_Vertical
Q1, Q2: 2N7002; SOT-23
R1, R2: 499k; R_1206_3216Metric_Pad1.42x1.75mm_HandSolder
R3: 49k9; R_1206_3216Metric_Pad1.42x1.75mm_HandSolder
R4, R17: 2k2; R_1206_3216Metric_Pad1.42x1.75mm_HandSolder
R5: 75k; R_1206_3216Metric_Pad1.42x1.75mm_HandSolder
R6: 24k; R_1206_3216Metric_Pad1.42x1.75mm_HandSolder
R7: 900; R_1206_3216Metric_Pad1.42x1.75mm_HandSolder
R8, R9: 100; R_1206_3216Metric_Pad1.42x1.75mm_HandSolder
R10: 1M; R_1206_3216Metric_Pad1.42x1.75mm_HandSolder
R11: 202k; R_1206_3216Metric_Pad1.42x1.75mm_HandSolder
R12, R16: 6k04; R_1206_3216Metric_Pad1.42x1.75mm_HandSolder
R13: 47k; R_1206_3216Metric_Pad1.42x1.75mm_HandSolder
R14: 3k3; R_1206_3216Metric_Pad1.42x1.75mm_HandSolder
R15: 10k; R_1206_3216Metric_Pad1.42x1.75mm_HandSolder
R18: PROV; R_1206_3216Metric_Pad1.42x1.75mm_HandSolder
U1: SPAN02A-12; SPAN02
U2: LM311; SOIC-8_3.9x4.9mm_P1.27mm
U3, U4: LR8K4-G; TO-252-2
U5: MOC8021; DIP-6_W7.62mm

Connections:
+12V: C3.1, D5.2, R5.2, R15.1, R17.1, U1.6, U2.8
/+HV: F2.1, J1.1
/VHI: J3.3, J3.4, U5.5
/Vin: D2.1, R2.2, R3.1, R9.2
/Vref: R5.1, R6.2, R8.2, R10.1
GND: C3.2, C4.2, C5.2, D2.2, J2.2, J4.2, Q1.2, Q2.2, R4.2, R7.1, R11.2, R13.2, U1.7, U2.1, U2.4
GNDPWR: C1.1, J3.2, U1.1, U5.4
unnamed: C1.2, D1.1, U1.2
unnamed: C2.1, R8.1, U2.2
unnamed: C2.2, R9.1, U2.3
unnamed: C4.1, R12.1, U3.2, U4.1
unnamed: C5.1, R16.1, R18.1, U4.2
unnamed: D1.2, J3.1
unnamed: D3.1, Q1.3, Q2.1
unnamed: D3.2, U5.2
unnamed: D4.1, U3.1
unnamed: D4.2, F2.2, R1.1
unnamed: D5.1, R14.1
unnamed: J4.1, R18.2
unnamed: Q1.1, R10.2, R15.2, U2.7
unnamed: Q2.3, R14.2
unnamed: R1.2, R2.1
unnamed: R3.2, R4.1
unnamed: R6.1, R7.2
unnamed: R11.1, R12.2, U3.3
unnamed: R13.1, R16.2, U4.3
unnamed: R17.2, U5.1
unnamed: U2.5, U2.6

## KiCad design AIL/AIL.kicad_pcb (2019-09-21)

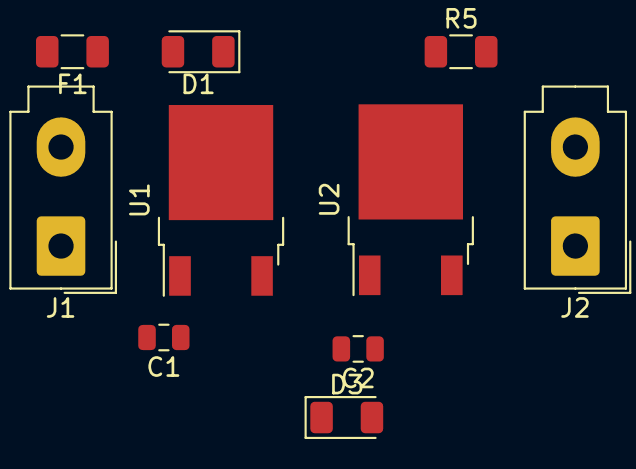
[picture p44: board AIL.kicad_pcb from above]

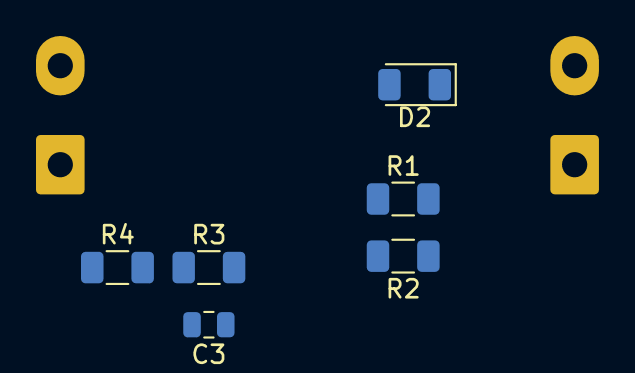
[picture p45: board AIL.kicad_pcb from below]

Board: 2 copper layers, 16 parts (6 on the bottom side), 9 nets, no tracks yet.

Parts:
C1: 10n; C_0805_2012Metric
C2, C3: 1uF; C_0805_2012Metric
D1, D2, D3: D; D_1206_3216Metric
F1: Polyfuse; Fuse_1206_3216Metric
J1: HV-IN; Molex_Mini-Fit_Jr_5566-02A_2x01_P4.20mm_Vertical
J2: AIL-OUT; Molex_Mini-Fit_Jr_5566-02A_2x01_P4.20mm_Vertical
R1, R3: 6k04; R_1206_3216Metric
R2: 202k; R_1206_3216Metric
R4: 47k; R_1206_3216Metric
R5: PROV; R_1206_3216Metric
U1, U2: LR8K4-G; TO-252-2

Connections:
unnamed: C1.1, D1.1, D2.1, U1.1
unnamed: C1.2, C2.2, C3.2, J1.2, J2.1, R2.1, R4.1
unnamed: C2.1, D2.2, D3.1, R1.2, U1.2, U2.1
unnamed: C3.1, D3.2, R3.2, R5.1, U2.2
unnamed: D1.2, F1.1
unnamed: F1.2, J1.1
unnamed: J2.2, R5.2
unnamed: R1.1, R2.2, U1.3
unnamed: R3.1, R4.2, U2.3

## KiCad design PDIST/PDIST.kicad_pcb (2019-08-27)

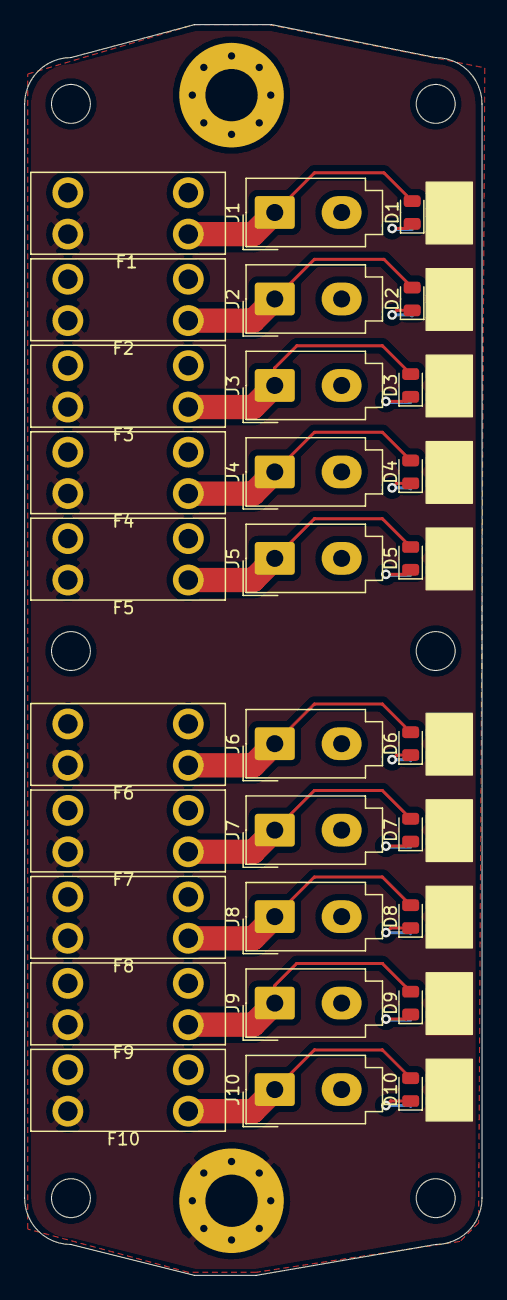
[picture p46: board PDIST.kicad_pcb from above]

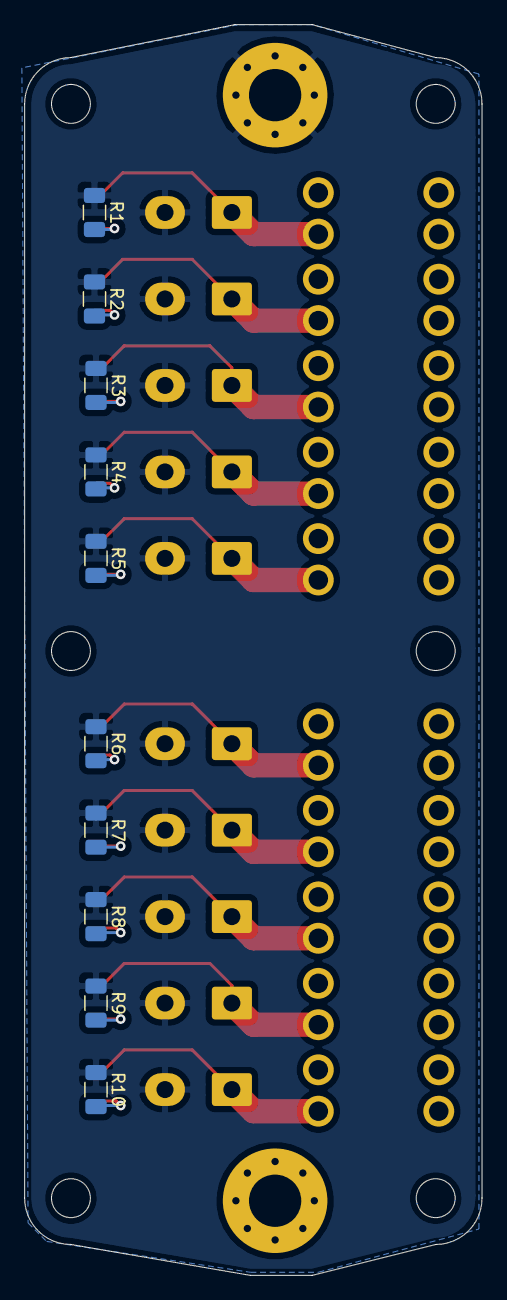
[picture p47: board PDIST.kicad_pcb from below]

Board: 2 copper layers, 37.6 x 102.9 mm, 42 parts (10 on the bottom side), 22 nets.

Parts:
D1, D2, D3, D4, D5, D6, D7, D8, D9, D10: LED; LED_0805_2012Metric
F1, F2, F3, F4, F5, F6, F7, F8, F9, F10: Fuse; Fuse-Mini_Blade-3568
H1, H2: MountingHole_Pad; MountingHole_4.3mm_M4_Pad_Via
J1, J2, J3, J4, J5, J6, J7, J8, J9, J10: Conn_01x02_Male; Molex_Mini-Fit_Jr_5566-02A_2x01_P4.20mm_Vertical
R1, R2, R3, R4, R5, R6, R7, R8, R9, R10: R; R_1206_3216Metric

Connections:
GND: H2.1, J1.2, J2.2, J3.2, J4.2, J5.2, J6.2, J7.2, J8.2, J9.2, J10.2, R1.1, R2.1, R3.1, R4.1, R5.1, R6.1, R7.1, R8.1, R9.1, R10.1
unnamed: D1.1, R1.2
unnamed: D1.2, F1.1, J1.1
unnamed: D2.1, R2.2
unnamed: D2.2, F2.1, J2.1
unnamed: D3.1, R3.2
unnamed: D3.2, F3.1, J3.1
unnamed: D4.1, R4.2
unnamed: D4.2, F4.1, J4.1
unnamed: D5.1, R5.2
unnamed: D5.2, F5.1, J5.1
unnamed: D6.1, R6.2
unnamed: D6.2, F6.1, J6.1
unnamed: D7.1, R7.2
unnamed: D7.2, F7.1, J7.1
unnamed: D8.1, R8.2
unnamed: D8.2, F8.1, J8.1
unnamed: D9.1, R9.2
unnamed: D9.2, F9.1, J9.1
unnamed: D10.1, R10.2
unnamed: D10.2, F10.1, J10.1
unnamed: F1.2, F2.2, F3.2, F4.2, F5.2, F6.2, F7.2, F8.2, F9.2, F10.2, H1.1

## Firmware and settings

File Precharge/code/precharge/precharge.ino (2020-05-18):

/*
  Precharge - Code to drive the NU Racing Precharge module (prototype)
  Created by Michael Ruppe
  April 2020

  Watch a primer video on this device here: https://youtu.be/6-RndXZ5mR4
  For more documentation, visit: https://github.com/michaelruppe/FSAE

  Dear future FSAE engineer,
  Perform a find (Ctrl+f) for "TODO" to see if I left you any surprises :D

  Commissioning notes:
    - Make sure TARGET_PERCENT is sensible (95%). I set it much lower
      during prototyping.

  Features:
    - Voltage feedback ensures sufficient precharge before closing AIR
    - Wiring fault / stuck-discharge detection on "too-fast/slow" precharge
    - May arrest AIR chatter -> minimum precharge time triggers error state and
      requires uC reset or power cycle.


  Other Notes:
    - Consider adding a condition to the STATE_STANDBY -> STATE_PRECHARGE
      transition: Check for near-zero TS voltages ensures full discharge before
      attempting a precharge.
*/


#include "gpio.h"
#include "measurements.h"
#include "moving-average.h"
#include "states.h"

const float MIN_SDC_VOLTAGE = 11.0; // [Volts]

// Exponential Moving Average Filters
MovingAverage TSV_Average(0, 0.1); // Tractive system Voltage
MovingAverage ACV_Average(0, 0.1); // Accumulator (upstream of precharge resistor)
MovingAverage SDC_Average(0, 0.5); // Shutdown Circuit

STATEVAR state = STATE_STANDBY;
STATEVAR lastState = STATE_UNDEFINED;
int errorCode = ERR_NONE;

StatusLight statusLED[4] {{ STATUS_LED[0] },
                          { STATUS_LED[1] },
                          { STATUS_LED[2] },
                          { STATUS_LED[3] }};

char lineBuffer[50];
unsigned long now; // Uptime from millis()

void setup() {
  Serial.begin(460800);
  setupGPIO();
  delay(3000);  // TODO: remove during commissioning

}


void loop() {
  now = millis();

  // Always monitor Shutdown Circuit Voltage and react
  monitorShutdownCircuit();

  // The State Machine
  switch(state){
    case STATE_STANDBY :
      standby();
      break;

    case STATE_PRECHARGE :
      precharge();
      break;

    case STATE_ONLINE :
      running();
      break;


    case STATE_ERROR :
      errorState();

    default : // You tried to enter a state not defined in this switch-case
      state = STATE_ERROR;
      errorCode |= ERR_STATE_UNDEFINED;
      errorState();
  }

  updateStatusLeds();

}

void monitorShutdownCircuit() {
  static unsigned long lastSample = 0;
  if (now > lastSample + 10) {
    lastSample = now;
    SDC_Average.update(getShutdownCircuitVoltage());
  }
  // Error state should be deadlocked - no way out.
  if ( SDC_Average.value() < MIN_SDC_VOLTAGE && state != STATE_ERROR) {
    state = STATE_STANDBY;
  }
}

// Open AIRs, Open Precharge, indicate status, wait for stable shutdown circuit
void standby() {
  static unsigned long epoch;
  if (lastState != STATE_STANDBY) {
    lastState = STATE_STANDBY;
    statusLEDsOff();
    statusLED[0].on();
    Serial.println(F(" === STANDBY"));
    Serial.println(F("* Waiting for stable shutdown circuit"));
    epoch = millis(); // make sure to reset if we've circled back to standby

    // Reset moving averages
    TSV_Average.reset();
    ACV_Average.reset();
    SDC_Average.reset();
  }

  // Disable AIR, Disable Precharge
  digitalWrite(PRECHARGE_CTRL_PIN, LOW);
  digitalWrite(SHUTDOWN_CTRL_PIN, LOW);

  // Check for stable shutdown circuit
  const unsigned int WAIT_TIME = 200; // ms to wait for stable voltage
  if (SDC_Average.value() >= MIN_SDC_VOLTAGE){
    if (millis() > epoch + WAIT_TIME){
      state = STATE_PRECHARGE;
    }
  } else {
    epoch = millis(); // reset timer
  }

}

// Close the precharge relay, monitor precharge voltage.
// Trip error if charge-time looks unusual
void precharge() {
  // Look for "too fast" or "too slow" precharge, indicates wiring fault
  const float MIN_EXPECTED = 500; // [ms]. Set this to something reasonable after collecting normal precharge sequence data
  const float MAX_EXPECTED = 3000; // [ms]. Set this to something reasonable after collecting normal precharge sequence data
  // If a precharge is detected faster than this, an error is
  // thrown - assumed wiring fault. This could also arrest oscillating or
  // chattering AIRs, because the TS will retain some amount of precharge.
  const float TARGET_PERCENT = 88.0;   // TODO: Requires suitable value during commissioning (eg 95%)
  const unsigned int SETTLING_TIME = 200; // [ms] Precharge amount must be over TARGET_PERCENT for this long before we consider precharge complete
  static unsigned long epoch;
  static unsigned long tStartPre;

  if (lastState != STATE_PRECHARGE){
    digitalWrite(PRECHARGE_CTRL_PIN, HIGH);
    lastState = STATE_PRECHARGE;
    statusLEDsOff();
    statusLED[1].on();
    sprintf(lineBuffer, " === PRECHARGE   Target precharge %4.1f%%\n", TARGET_PERCENT);
    Serial.print(lineBuffer);
    epoch = now;
    tStartPre = now;
  }

  // Sample the voltages and update moving averages
  const unsigned long samplePeriod = 10; // [ms] Period to measure voltages
  static unsigned long lastSample = 0;
  if (now > lastSample + samplePeriod){  // samplePeriod and movingAverage alpha value will affect moving average response.
    lastSample = now;
    ACV_Average.update(getAccuVoltage());
    TSV_Average.update(getTsVoltage());
  }
  double acv = ACV_Average.value();
  double tsv = TSV_Average.value();

  // The precharge progress is a function of the accumulator voltage
  double prechargeProgress = 100.0 * tsv / acv; // [%]

  // Print Precharging progress
  static unsigned long lastPrint = 0;
  if (now >= lastPrint + 100) {
    lastPrint = now;
    sprintf(lineBuffer, "%5lums %4.1f%%   %5.1fV\n", now-tStartPre, prechargeProgress, TSV_Average.value());
    Serial.print(lineBuffer);
  }

  // Check if precharge complete
  if ( prechargeProgress >= TARGET_PERCENT ) {
    // Precharge complete
    if (now > epoch + SETTLING_TIME){
      state = STATE_ONLINE;
      sprintf(lineBuffer, "* Precharge complete at: %2.0f%%   %5.1fV\n", prechargeProgress, TSV_Average.value());
      Serial.print(lineBuffer);
    }
    else if (now < tStartPre + MIN_EXPECTED && now > epoch + SETTLING_TIME) {    // Precharge too fast - something's wrong!
      state = STATE_ERROR;
      errorCode |= ERR_PRECHARGE_TOO_FAST;
    }

  } else {
    // Precharging
    epoch = now;

    if (now > tStartPre + MAX_EXPECTED) {       // Precharge too slow - something's wrong!
      state = STATE_ERROR;
      errorCode |= ERR_PRECHARGE_TOO_SLOW;
    }
  }



}

void running() {
  const unsigned int T_OVERLAP = 500; // ms. Time to overlap the switching of AIR and Precharge
  static unsigned long epoch;
  if (lastState != STATE_ONLINE){
    statusLEDsOff();
    statusLED[2].on();
    Serial.println(F(" === RUNNING"));
    lastState = STATE_ONLINE;
    epoch = now;
  }

  digitalWrite(SHUTDOWN_CTRL_PIN, HIGH);
  if (now > epoch + T_OVERLAP) digitalWrite(PRECHARGE_CTRL_PIN, LOW);

}

void errorState() {
  digitalWrite(PRECHARGE_CTRL_PIN, LOW);
  digitalWrite(SHUTDOWN_CTRL_PIN, LOW);

  if (lastState != STATE_ERROR){
    lastState = STATE_ERROR;
    statusLEDsOff();
    statusLED[3].update(50,50); // Strobe STS LED
    Serial.println(F(" === ERROR"));

    // Display errors: Serial and Status LEDs
    if (errorCode == ERR_NONE){
      Serial.println(F("   *Error state, but no error code logged..."));
    }
    if (errorCode & ERR_PRECHARGE_TOO_FAST) {
      Serial.println(F("   *Precharge too fast. Suspect wiring fault / chatter in shutdown circuit."));
      statusLED[0].on();
    }
    if (errorCode & ERR_PRECHARGE_TOO_SLOW) {
      Serial.println(F("   *Precharge too slow. Potential causes:\n   - Wiring fault\n   - Discharge is stuck-on\n   - Target precharge percent is too high"));
      statusLED[1].on();
    }
    if (errorCode & ERR_STATE_UNDEFINED) {
      Serial.println(F("   *State not defined in The State Machine."));
    }
  }

}


// Loop through the array and call update.
void updateStatusLeds() {
  for (uint8_t i=0; i<(sizeof(statusLED)/sizeof(*statusLED)); i++){
    statusLED[i].update();
  }
}
void statusLEDsOff() {
  for (uint8_t i=0; i<(sizeof(statusLED)/sizeof(*statusLED)); i++){
    statusLED[i].off();
  }
}
void updateStatusLeds(long ton, long toff) {
  for (uint8_t i=0; i<(sizeof(statusLED)/sizeof(*statusLED)); i++){
    statusLED[i].update(ton, toff);
  }
}

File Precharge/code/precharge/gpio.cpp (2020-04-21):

#include "gpio.h"

void setupGPIO(void) {
    // Configuration solder-jumpers
    for (uint8_t i=0; i<(sizeof(CONFIG_PIN)/sizeof(*CONFIG_PIN)); i++){
      pinMode(CONFIG_PIN[i], INPUT);
      digitalWrite(CONFIG_PIN[i], HIGH); // Activate pullup
    }

    pinMode(SHUTDOWN_CTRL_PIN, OUTPUT);
    digitalWrite(SHUTDOWN_CTRL_PIN, LOW);

    pinMode(PRECHARGE_CTRL_PIN, OUTPUT);
    digitalWrite(PRECHARGE_CTRL_PIN, LOW);

    pinMode(FREQ_TS_PIN, INPUT);
    pinMode(FREQ_ACCU_PIN, INPUT);
    pinMode(PDOC_PIN, INPUT);
    pinMode(PWR_OK_PIN, INPUT);

}

// TODO: Why does the voltae calculation read consistently low?
// I have a bandaid fix in place here but the fit will not be super-accurate (diode)
float getShutdownCircuitVoltage() {
  const float VF_DIODE = 0.7;
  const float GAIN_PWR_OK_DIVIDER = 0.2537;
  const float ADC_PREC = 3.3 / 1023.0; // ADC precision: full scale is 3.3V @ 1023
  unsigned int raw = analogRead(PWR_OK_PIN);
  // return (float)raw * ADC_PREC / GAIN_PWR_OK_DIVIDER + VF_DIODE; // TODO: Why does this read incorrectly?
  return map((float)raw*ADC_PREC,0,2.12,0,11.96); // poor fit, experimental. Disregards diode but the ideal formula did not work...
}


// A class for easily controlling the status lights on board.
// Make sure you call update() every loop.
StatusLight::StatusLight(int pin) {
  ledPin = pin;
  pinMode(ledPin, OUTPUT);

  OnTime = 0;
  OffTime = 0;

  ledState = LOW;
  previousMillis = 0;
}

void StatusLight::update() {
  // check to see if it's time to change the state of the LED
  unsigned long currentMillis = millis();

  if( (OnTime == 0 || ledState == HIGH) && (currentMillis - previousMillis >= OnTime))
  {
  	ledState = LOW;  // Turn it off
    previousMillis = currentMillis;  // Remember the time
    digitalWrite(ledPin, ledState);  // Update the actual LED
  }
  else if ( (OffTime == 0 || ledState == LOW) && (currentMillis - previousMillis >= OffTime)) {
    ledState = HIGH;  // turn it on
    previousMillis = currentMillis;   // Remember the time
    digitalWrite(ledPin, ledState);	  // Update the actual LED
  }
}

// Set the frequency and duty-cycle by defining on-time and off-time [ms]
void StatusLight::update(long on, long off) {
  OnTime = on;
  OffTime = off;
  // previousMillis = 0; // Guarantee an update NOW
  // ^ Removed: if user calls this form of update repeatedly by accident,
  // the LED behaciour will be erratic.
  update();
}

// Set the LED on
void StatusLight::on() {
  OnTime = 500; // Must be greater than zero.
  OffTime = 0;  // Must be zero
}

// Set the LED off
void StatusLight::off() {
  OnTime = 0;  // Must be zero
  OffTime = 500; // Must be greater than zero.

}

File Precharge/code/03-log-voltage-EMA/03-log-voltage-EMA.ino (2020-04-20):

// Run a precharge cycle and log the voltages to console for plotting

#include "gpio.h"
#include "measurements.h"
#include "moving-average.h"
// CAN Libraries
// #include <circular_buffer.h>
// #include <FlexCAN_T4.h>
// #include <imxrt_flexcan.h>
// #include <kinetis_flexcan.h>


unsigned long startTime;


MovingAverage TractiveSystemVoltage(0,0.1);
MovingAverage AccumulatorVoltage(0,0.1);


void setup() {
  Serial.begin(460800);
  // Initialise IO
  setupGPIO();
  delay(3000);
  startTime = millis() + 1500;
  Serial.println("Time(ms),Vaccu,Vts");

}


void loop() {

  unsigned long now = millis();
  const unsigned long durationCharge = 6000;   // duration to precharge
  const unsigned long durationExperiment = 25000;   // total experiment duration


  // precharge contactor switching
  if (now < startTime || now > startTime + durationCharge) {
    digitalWrite(PRECHARGE_CTRL_PIN, LOW);
  } else {
    digitalWrite(PRECHARGE_CTRL_PIN, HIGH);
  }

  if (now < startTime + durationExperiment) {

    // double fAccu = getFrequency(FREQ_ACCU_PIN);
    // double fTs = getFrequency(FREQ_TS_PIN);
    TractiveSystemVoltage.update( getTsVoltage() );
    AccumulatorVoltage.update( getAccuVoltage() );
    // double vAccu = getAccuVoltage();
    // double vTs = getTsVoltage();

    Serial.print((long)now - (long)startTime);
    Serial.print(",");
    // Serial.print(fAccu);
    // Serial.print(",");
    // Serial.print(fTs);
    // Serial.print(",");
    Serial.print(AccumulatorVoltage.value());
    Serial.print(",");
    Serial.print(TractiveSystemVoltage.value());

    Serial.println();
  }

}

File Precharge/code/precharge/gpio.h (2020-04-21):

// Pin definitions for the project

#ifndef PINDEFS_H
#define PINDEFS_H
#include "Arduino.h"
#include <stdint.h>

class StatusLight
{
  public:
    StatusLight(int pin);
    void update();
    void update(long on, long off);
    void on();
    void off();
  private:
    int ledPin;
    long OnTime;
    long OffTime;
    int ledState;
    unsigned long previousMillis;
};

// Configuration solder-jumpers
const int CONFIG_PIN[] = {4,5,6};
// Status LEDs
const int STATUS_LED[] = {0,1,2,3};

// Relays
const int SHUTDOWN_CTRL_PIN = 11;
const int PRECHARGE_CTRL_PIN = 12;

// Frequency measurements (from Voltage-to-Frequency converters)
const int FREQ_ACCU_PIN = 14;
const int FREQ_TS_PIN = 15;

// Status inputs
const int PDOC_PIN = A7; // Active-high when PDOC is OK
const int PWR_OK_PIN = A4; // Active-high when power-supply (shutdown circuit) is OK

// Function prototypes
void setupGPIO(void);
float getShutdownCircuitVoltage(void);


#endif

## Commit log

2019-08-14 Update TSAL-HVM to v1.1
    Move indicator LED text to silk layer
    Fix wayward trace HV- to GND
    [TSAL-DRV.kicad_pcb, TSAL-DRV.sch, TSAL-HVM.kicad_pcb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]
2019-08-14 Add Hard Fault Latch board
    [HFL.kicad_pcb, HFL.sch]
2019-08-15 Update HFL - include indicator lamp outputs (low-side)
    [HFL.kicad_pcb, HFL.sch]
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2019-08-15 Update schematic title blocks, READMEs, Schematic.pdfs
    [TSAL-DRV.sch, TSAL-HVM.kicad_pcb, TSAL-HVM.sch]
2019-08-20 Finalise HFL v1
    [HFL.kicad_pcb, HFL.sch]
2019-08-27 commit before revising some pcbs
    [PDIST.kicad_pcb, PDIST.sch, TSAL-DRV.sch]
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2019-08-28 update j2 pinout to match CCU board
    [HFL.kicad_pcb, HFL.sch]
2019-08-31 Update TSAL-HVMv1.1 with lessons learned from assembling v1
    [TSAL-HVM.kicad_pcb, TSAL-HVM.sch]
2019-09-01 Update schematic revision to 1.1
    [TSAL-HVM.sch]
2019-09-01 Update schematic pdf and PCB render to 1.1
    [TSAL-HVM.sch]
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2019-09-01 PCB: Remove routed slot. Update render
    [TSAL-HVM.kicad_pcb]
2019-09-01 Update schematic labels and README
    [TSAL-HVM.sch]
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2019-09-03 Aesthetic upgrades to schematic, render
    [TSAL-DRV.kicad_pcb, TSAL-DRV.sch]
2019-09-04 update TSAL PCB v1.1
    [TSAL-HVM.kicad_pcb]
2019-09-04 add Accumulator Indicator - preliminary design
    [AIL.kicad_pcb, AIL.sch]
2019-09-21 Add AIL schematic. Add TSAL-DRV pinout diagram
    [AIL.kicad_pcb, AIL.sch]
2019-09-22 Update TSAL to v2. Add AIL
    [TSAL-HVM.kicad_pcb, TSAL-HVM.sch]
2019-09-23 Update TSAL with connector 3D models
    [10-pin-mini-fit-jr.stp, 12-pin-mini-fit-jr.stp, 14-pin-mini-fit-jr.stp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]
2019-10-01 Update HFL schematic to use logic chips instead of relay latching-logic
    [HFL.sch]
2019-10-02 Update HFL with additional commissioning features
    [HFL.sch]
2019-10-02 Update HFL PCB - preliminary component placement
    [HFL.kicad_pcb, HFL.sch]
2019-10-02 Update HFL PCB Faults and statuses now independent. Working on part placement
    [HFL.kicad_pcb, HFL.sch]
2019-10-03 Update HFL - tentatively complete v2 routing still need to select parts
    [10-pin-mini-fit-jr.stp, 12-pin-mini-fit-jr.stp, 14-pin-mini-fit-jr.stp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]
2019-10-09 Cosmetic upgrades to HFL v2
    also scattered some GND-GND vias
    [HFL.kicad_pcb, HFL.sch]
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2019-10-09 Update to v2.1
    cosmetic changes to silkscreen. Remove power input fuse
    [TSAL-HVM.kicad_pcb, TSAL-HVM.sch]
2019-10-09 Add MOBO: Sketch-out motherboard idea
    [MOBO.kicad_pcb, MOBO.sch]
2019-10-09 Update net labels and minor power routing in v2.1
    [TSAL-HVM.kicad_pcb, TSAL-HVM.sch]
2019-10-10 Update HFL - pcb silk
    [HFL.kicad_pcb, HFL.sch]
2019-10-10 Update TSAL-DRV to v2 schematic and select parts. Need route board
    [10-pin-mini-fit-jr.stp, 12-pin-mini-fit-jr.stp, 14-pin-mini-fit-jr.stp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]
2019-10-29 Add CELL-MOUNT FR4 design
    For mounting cells in accumulator
    [CELL-MOUNT.kicad_pcb, CELL-MOUNT.sch]
2019-12-11 Update TSAL versioning, renders and schematic prints
    [TSAL-DRV.kicad_pcb, TSAL-DRV.sch, TSAL-HVM.sch]
2020-01-22 Lock down before branch for projects
    [CELL-MOUNT.kicad_pcb, HFL.kicad_pcb]
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2020-01-27 create precharge and prelim simulations
    [Calculations.xlsx, Precharge.sch]
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2020-01-29 Precharge: update schematic to uController preliminary
    [Precharge.sch]
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2020-03-03 Update precharge design. Begin PCB layup
    [Precharge.kicad_pcb, Precharge.sch]
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2020-03-03 add mini-fit-jr STEP files
    [10-pin-mini-fit-jr.stp, 12-pin-mini-fit-jr.stp, 14-pin-mini-fit-jr.stp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]
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2020-03-16 update precharge schematic + pcb
    [HSA25.igs, Precharge.kicad_pcb, Precharge.sch]
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2020-03-17 🛀 cleanup unsued .stp files
    [10-pin-mini-fit-jr.stp, 12-pin-mini-fit-jr.stp, 14-pin-mini-fit-jr.stp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]
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2020-03-18 :straight_ruler: spec frequency optocouplers properly
    [Precharge.sch]
2020-03-18 :hammer: fix LM331 circuits (Voltage-frequency)
    [Precharge.sch]
2020-03-18 :hammer: position components, add CAD models
    [430450812.stp, G2RL_24.step, Precharge.kicad_pcb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]
2020-03-18 :hourglass_flowing_sand: hand-route crucial sections
    [Precharge.kicad_pcb, Precharge.sch]
2020-03-19 :pencil: Add connector cad files and associate with footprints.
    [39281043.stp, 430450212.stp, Precharge.kicad_pcb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]
2020-03-19 :pencil2: manual route the critical paths
    [Precharge.kicad_pcb, Precharge.sch]
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2020-03-21 :pencil: Add title-block info
    [Precharge.sch]
2020-03-21 🔩 Connect CAN transceiver S->GND
    [Precharge.kicad_pcb, Precharge.sch]
2020-03-21 :pencil: correctly initialise GPIO inputs with pullups
    [gpio.cpp, gpio.h]
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2020-04-19 :star: add V-F Experiment
    [Calculations.xlsx]
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2020-04-20 :hammer: add moving average filter and experiment
    [Calculations.xlsx]
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2020-04-20 :star: Working state machine
    Ready for commissioning and finding all the bugs :D
    [precharge.ino]
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2020-04-21 :bathtub: fix string format for precharge progress
    [precharge.ino]
2020-04-21 :pencil2: update error status light behaviour
    [precharge.ino]
2020-04-21 :hammer: reset moving averages prevents errors, better formatted strings
    [precharge.ino]
2020-04-21 :hammer: only reset moving average when ENTERING the state.
    Also, add a sample rate to the shutdown circuit
    [precharge.ino]
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2020-04-22 :pencil: Update commissioning notes
    [Experiments.xlsx]
2020-04-22 :hammer: update component values to prototype as-built
    [Precharge.sch]
2020-04-22 :hammer: update board routing to reflect bodges made in prototyping
    [Precharge.kicad_pcb, Precharge.sch]
2020-04-22 :pencil: document precharge resistor selection
    [Experiments.xlsx]
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2020-04-29 :hammer: update PDOC component value - reference voltage
    [Precharge.sch]
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2020-04-30 :update TSALv3: schematic (cosmetic)
    remove note on D2 - this should ALWAYS be populated
    increment version to v3.1 - no physical changes, only the important removal of note on D2
    [TSALv3.sch]
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2020-05-29 :hammer: Fix error with 555 timer
    [HFL.sch]
2025-12-08 update project for KiCad 9.x
    [TSALv3.kicad_pcb, TSALv3.kicad_sch, TSALv3.sch]
